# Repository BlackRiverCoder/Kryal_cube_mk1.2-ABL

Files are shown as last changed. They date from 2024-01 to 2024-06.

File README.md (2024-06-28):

# Kryal_cube_mk1.2-ABL

+ Today I am building ABL sensor to 3d printer Kryal Cube mk1.2 
+ In this solution we're using Z Endstop as calibration switch that means, we don't need Z Endstop anymore
+ Calibration will start before every print
+ The disadvantage is that you must install the sensor next to the extruder and after calibration remove it

## Repository architecture:
 - [**Manuals**](#manuals-to-install-abl-on-kryal-cube-mk12)
 - [**Models**](#models)
 - [**Nozzle_to_probe_offset**](#nozzle_to_probe_offset)
 - [**Troubleshooting**](#troubleshooting)
 - [**Sources**](#sources)
 - [**Troubleshooting Sources**](#troubleshooting-sources)

## Manuals to install ABL on Kryal Cube mk1.2:
 
**- 1.)** [English manual](#english-manual)

**- 2.)** [Slovak Manual](#slovak-manual)

## Models:

  - Formats: **.stl** and for SolidWorks **.sldprt**

+ **Right side model used with original extruder: ([ModelR-O v1.0](https://github.com/BlackRiverCoder/Kryal_cube_mk1.2-ABL/tree/main/Assests/Models/ModelR-O%20v1.0))**
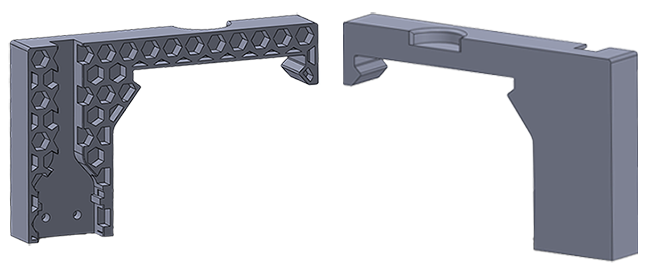
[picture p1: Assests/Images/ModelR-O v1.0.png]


+ **Left side model used with original extruder: ([ModelL-O v1.0](https://github.com/BlackRiverCoder/Kryal_cube_mk1.2-ABL/tree/main/Assests/Models/ModelL-O%20v1.0))**
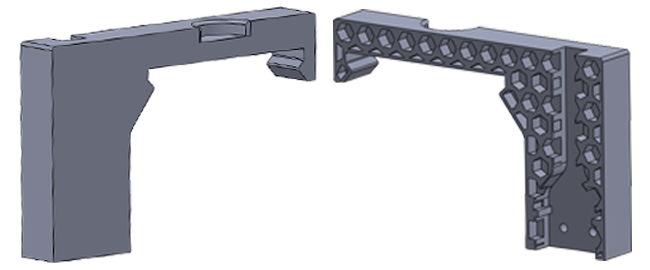
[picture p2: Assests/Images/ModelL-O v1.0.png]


+ **Left side model used with E3D extruder: ([ModelL-E3D v1.0](https://github.com/BlackRiverCoder/Kryal_cube_mk1.2-ABL/tree/main/Assests/Models/ModelL-E3D%20v1.0))**
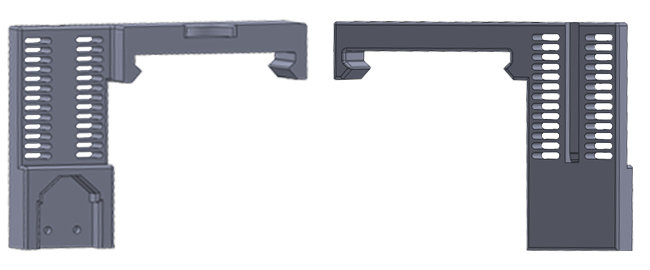
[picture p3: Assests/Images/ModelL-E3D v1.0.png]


+ **Magnetic models used with E3D extruder: ([ModelM-E3D v1.0](https://github.com/BlackRiverCoder/Kryal_cube_mk1.2-ABL/tree/main/Assests/Models/ModelM-E3D%20v1.0))**
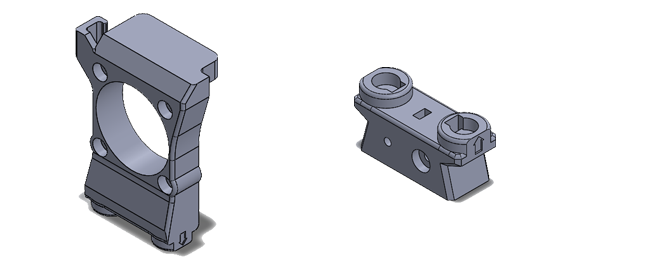
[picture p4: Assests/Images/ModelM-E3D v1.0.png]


## English Manual:

***1.) Hardware preparation:***
 - 1.) **Things we need:**
    - NC Switch
    - Cables
    - Switch holder (according to the side on which the switch will be and according to the extruder type) you can download models [here](https://github.com/BlackRiverCoder/Kryal_cube_mk1.2-ABL/tree/main/Assests/Models) and every model types and images are [here](#models)
    - Some connectors
    - Screws to attach the switch to the holder
    - Magnets 6x3mm (for magnet type ABL)

 - 2.) **Assembling the holder:**
    **Fixed type:**
    - 1.) Solder wires to the C and NC on the switch and at the end of the cable make connector of your choice (as you can see in the red circle (female type))
    - 2.) With the screws attach the switch to the 3d printed model
    - _Your holder should look like this one:_
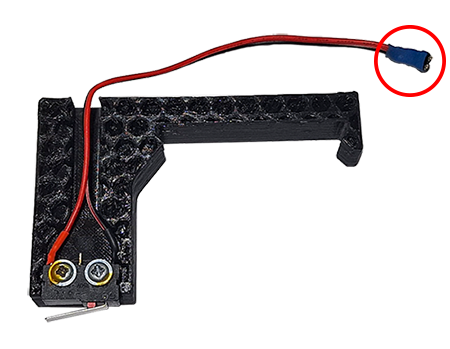
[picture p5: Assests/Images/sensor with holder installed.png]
    

    **Magnet type:**
    - 1.) Insert magnets to both models (Double check the magnet faces, if you don't put them in correct way, they won't snap together)
    - 2.) Attach the microswitch to the microswitch holder and put screws to hold it
    - 3.) Attach cables to the main holder

 - 3.) **Connect cables to the main board:**
    - Pull the cable along 3d printer case, from extruder, where you make another (male type) connector, to the main board
    - Kryal Cube mk1.2 using AtMega2560 with RAMPS14, so connect the switch to these pins:
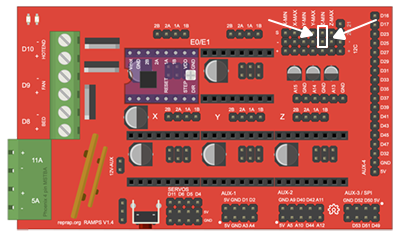
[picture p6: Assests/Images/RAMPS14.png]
   

 - **Final - calibration sensor installed next to the extruder:**
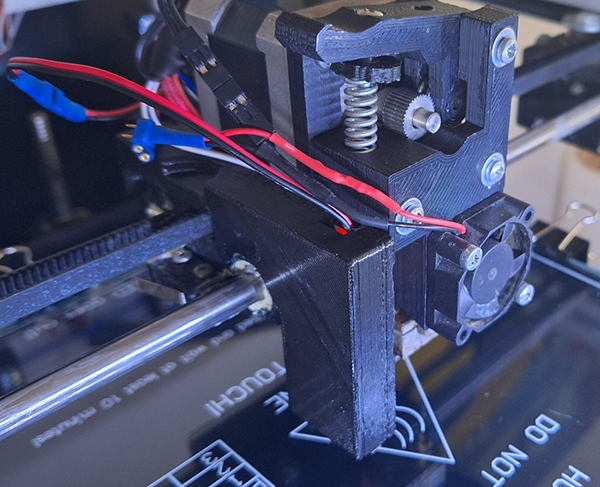
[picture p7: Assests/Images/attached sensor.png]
   

***2.) Firmware configuration:***
 > [!IMPORTANT]
 > Marlin version - 2.0.9.2, in other versions settings can be different.
 - 1.) **Disabling settings:**
   - If you have enabled any of these settings, please disable them using // before every **#define**:
      - **Configuration.h**
        ```
        #define PROBE_MANUALLY
        ```
        ```
        #define AUTO_BED_LEVELING_3POINT
        ```
        ```
        #define AUTO_BED_LEVELING_LINEAR
        ```
        ```
        #define AUTO_BED_LEVELING_UBL
        ```
        ```
        #define MESH_BED_LEVELING
        ```
        ```
        #define RESTORE_LEVELING_AFTER_G28
        ```
        ```
        #define ENABLE_LEVELING_AFTER_G28
        ```
        ```
        #define LCD_BED_LEVELING
        ```
        
      - **Configuration_adv.h**
        ```
        #define BABYSTEP_DISPLAY_TOTAL
        ```
 > [!WARNING]
 > If you don't disable these settings and try to build the code, you can get errors!

 - 2.) **Enabling/configuring settings:**
    - Enable settings removing // before **#define**
      - **Configuration.h**
        - !! Set dimensions where the nozzle is safely on the bed and bed sizes !!
        - EEPROM settings:
          ```
          #define EEPROM_SETTINGS
          ```
          ```
          #define EEPROM_AUTO_INIT
          ```
        - Z Safe homing:
          ```
          #define Z_SAFE_HOMING
          ```
          ```
          #define Z_HOMING_HEIGHT  30
          ```
          ```
          #define Z_AFTER_HOMING   20
          ```
        - ABL:
          - -left +right; -front +back; -down (our solution only has down); these settings can be found [here](#nozzle_to_probe_offset)
          ```
          #define NOZZLE_TO_PROBE_OFFSET { -32, -15, -7 }
          ```
          ```
          #define AUTO_BED_LEVELING_BILINEAR
          ```
          ```
          #define FIX_MOUNTED_PROBE
          ```
          ```
          #define Z_MIN_PROBE_USES_Z_MIN_ENDSTOP_PIN
          ```
          - x*x = number of calibrating points
          ```
          #define GRID_MAX_POINTS_X x
          ```
          - safe distance from each edge of the bed
          ```
          #define PROBING_MARGIN 6
          ```
          ```
          - #define MULTIPLE_PROBING 2
          ```
          - higher speed = more inaccurate calibration
          ```
          #define Z_PROBE_FEEDRATE_SLOW (Z_PROBE_FEEDRATE_FAST / 3)
          ```
          ```
          #define Z_CLEARANCE_DEPLOY_PROBE   10
          ```
          ```
          #define Z_CLEARANCE_BETWEEN_PROBES 10
          ```
          ```
          #define Z_CLEARANCE_MULTI_PROBE     3
          ```
          ```
          #define Z_AFTER_PROBING            30
          ```
          ```       
          #define Z_PROBE_LOW_POINT          -5
          ```

      - **Configuration_adv.h**
        ```
        #define BABYSTEPPING
        ```
        ```
        #define DOUBLECLICK_FOR_Z_BABYSTEPPING
        ```
        ```
        #define BABYSTEP_ZPROBE_OFFSET
        ```
        - This is coreXY 3d printer, so BABYSTEP Graphic Overlay is flipped (Symbol up = bed down; Symbol down = bed up)
        ```
        #define BABYSTEP_ZPROBE_GFX_OVERLAY
        ```
        - When trying to calibrate, on the last line the extruder head was rubbing against the back of the 3d printer frame, so I'm setting the limit from the back side
        ```
        #define PROBING_MARGIN_BACK PROBING_MARGIN +15
        ```
        ```
        #define DEFAULT_STEPPER_DEACTIVE_TIME 400
        ```
      
***3.) Building and flashing the firmware:***
 > [!WARNING]
 > If you have been using the Z Probe settings, reset them via "Configuration", "Restore Settings" and then "Store Settings" on the 3d printer display!
 > You can avoid many problems!

 > [!CAUTION]
 > Flashing the firmware is the most dangerous part, so double-check everything! (Code, USB connection).
 > While flashing, printer must be powered up!

 - 1.) **In VisualCode click build code, if the build is successful, you can write.**

 > [!NOTE]
 > On this printer with AtMega2560 you don't need bootloader, so flash with smile :)
 - 2.) **Now click flash.**
 - 3.) **If the flash was successful, restart the printer.**
 - 4.) **After printer starts up, go to "Configuration", "Restore Setting" and than "Store Settings", with these you store new settings to EEPROM**

***4.) Modify start GCode:***
 + **PrusaSlicer:**
 ```
 M0 Install probe ; Printer will wait until you install probe to the printer

 M140 S[first_layer_bed_temperature] ; Set bed temperature
 M190 S[first_layer_bed_temperature] ; Wait for bed temperature

 G28 ; Home all
 G29 ; Calibration

 M0 Remove probe ; Printer will wait until you remove probe from printer

 M104 S[first_layer_temperature] T0; Set nozzle temperature
 M109 S[first_layer_temperature] T0; Wait for nozzle temperature
 ```

 + **Orca Slicer:**
 ```
 M0 Install probe ; Printer will wait until you install probe to the printer

 M140 S[hot_plate_temp_initial_layer] ; Set bed temp
 M190 S[hot_plate_temp_initial_layer] ; Wait for bed temp

 G28 ; Home all
 G29 ; Calibration

 M0 Remove probe ; Printer will wait until you remove probe to the printer

 M104 S[nozzle_temperature_initial_layer] T0; Set nozzle temp
 M109 S[nozzle_temperature_initial_layer] T0; Wait for nozzle temp
 ```

## Slovak Manual:

***1.) Príprava hardware:***
 - 1.) **Veci, ktoré budeme potrebovať:**
    - NC Spínač
    - Káble
    - Držiak spínača (podľa strany, kde spínač bude a podľa typu extrudera) si môžeš stiahnuť modely [tu](https://github.com/BlackRiverCoder/Kryal_cube_mk1.2-ABL/tree/main/Assests/Models) a pozrieť si každý model s obrázkami [tu](#models)
    - Konektory
    - Šrubky na prichitenie spínača na držiak
    - Magnety 6x3mm (pre magnetický typ ABL)

 - 2.) **Skladanie držiaku snímača:**
    **Pevný typ:**
    - 1.) Prispájkovať káble na C a NC na spínači a na konci kábla urobiť konektor tvojej voľby (viď. červený kruh (female type))
    - 2.) Pomocou šrubiek pripevniť spínač na 3d vytlačený držiak
    - _Malo by to vyzerať nejako takto:_
    

    **Magnetický typ:**
    - 1.) Vlož magnety do obidvoch modelov (Dvakrát skontroluj otočenie magnetov, ak sa dajú opačne, neprichytia sa o seba)
    - 2.) Pripevni microspínač do držiaka microspínača a upevni ho šrubami
    - 3.) Pripevni káble do hlavného modelu

  - 3.) **Pripojenie káblov k základnej doske:**
     - Natiahni káble pozdĺž rámu 3d tlačiarne, od extrudera, kde urobíš opačný konektor pre kábel (male type) k základnej doske
     - Kryal Cube mk1.2 používa AtMega2560 s RAMPS14, takže spínač zapojíme na tieto piny:
     

  - **Ukážka pripevneného senzora vedľa extrudera:**
     

***2.) Configurácia Firmware:***
 > [!IMPORTANT]
 > Marlin verzia - 2.0.9.2, v iných verziách môžu byť nastavenia iné.
 - 1.) **Vypínanie nastavení:**
   - Ak máš v Marline povolené niečo z týchto nastavení, prosím vypni ich pomocou // pred každým **#define**:
      - **Configuraion.h**
        ```
        #define PROBE_MANUALLY
        ```
        ```
        #define AUTO_BED_LEVELING_3POINT
        ```
        ```
        #define AUTO_BED_LEVELING_LINEAR
        ```
        ```
        #define AUTO_BED_LEVELING_UBL
        ```
        ```
        #define MESH_BED_LEVELING
        ```
        ```
        #define RESTORE_LEVELING_AFTER_G28
        ```
        ```
        #define ENABLE_LEVELING_AFTER_G28
        ```
        ```
        #define LCD_BED_LEVELING
        ```

      - **Configuration_adv.h**
        ```
        #define BABYSTEP_DISPLAY_TOTAL
        ```
> [!WARNING]
> Ak nevypneš tieto nastavenia a dáš build code, môžu nastať chyby!

 - 2.) **Povoľovanie/konfigurácia nastavení:**
    - Nastavenia povolíš vymazaním // pred každým **#define**
      - **Configuration.h**
        - !! Nastav veľkosti, kde je tryska bezpečne nad podložkou a veľkosť podložky !!
        - EEPROM nastavenia:
          ```
          #define EEPROM_SETTINGS
          ```
          ```
          #define EEPROM_AUTO_INIT
          ```
        - Z Safe Homing:
          ```
          #define Z_SAFE_HOMING
          ```
          ```
          #define Z_HOMING_HEIGHT  30
          ```
          ```
          #define Z_AFTER_HOMING   20
          ```
        - ABL:
          - -vľavo +vpravo; -dopredu +dozadu; -dole (naše riešenie bude mať hodnotu len -dole, nie hore); tieto nastavenia nájdeš [tu](#nozzle_to_probe_offset)
          ```
          #define NOZZLE_TO_PROBE_OFFSET { -32, -15, -7 }
          ```
          ```
          #define AUTO_BED_LEVELING_BILINEAR
          ```
          ```
          #define FIX_MOUNTED_PROBE
          ```
          ```
          #define Z_MIN_PROBE_USES_Z_MIN_ENDSTOP_PIN
          ```
          - x*x = počet kalibračných bodov
          ```
          #define GRID_MAX_POINTS_X x
          ```
          - bezpečná vzdialenosť od každého kraja podložky
          ```
          #define PROBING_MARGIN 6
          ```
          ```
          - #define MULTIPLE_PROBING 2
          ```
          - vyššia rýchlosť = menej presná kalibrácia
          ```
          #define Z_PROBE_FEEDRATE_SLOW (Z_PROBE_FEEDRATE_FAST / 3)
          ```
          ```
          #define Z_CLEARANCE_DEPLOY_PROBE   10
          ```
          ```
          #define Z_CLEARANCE_BETWEEN_PROBES 10
          ```
          ```
          #define Z_CLEARANCE_MULTI_PROBE     3
          ```
          ```
          #define Z_AFTER_PROBING            30
          ```
          ```       
          #define Z_PROBE_LOW_POINT          -5
          ```

      - **Configuration_adv.h**
        ```
        #define BABYSTEPPING
        ```
        ```
        #define DOUBLECLICK_FOR_Z_BABYSTEPPING
        ```
        ```
        #define BABYSTEP_ZPROBE_OFFSET
        ```
        - Keďže táto tlačiareň je coreXY, BABYSTEP Graphic Overlay je otočený (Symbol hore = bed dole; Symbol dole = bed hore)
        ```
        #define BABYSTEP_ZPROBE_GFX_OVERLAY
        ```
        - Pri pokuse o kalibráciu sa na poslednom riadku hlava extrudéra otierala o zadnú časť rámu 3d tlačiarne, takže nastavujem limit zo zadnej strany
        ```
        #define PROBING_MARGIN_BACK PROBING_MARGIN +15
        ```
        ```
        #define DEFAULT_STEPPER_DEACTIVE_TIME 400
        ```

***3.) Build a flashovanie firmware:***
 > [!WARNING]
 > Ak si používal Z Probe nastavenia, resetuj ich cez "Configuration", "Restore Settings" a potom "Store Settings" na displeji 3d tlačiarne!
 > Zabrániš tak veľa problémom!

 > [!CAUTION]
 > Flashovanie firmware je tá najbezpečnejšia časť, takže všetko 2-krát skontroluj (Kód, USB pripojenie)
 > Počas flahovania musí byť tlačiareň napájaná!
  
 - 1.) **Vo VisualCode klikni na build code, ak bol build úspešný, môžeš flashovať.**

 > [!NOTE]
 > Na tejto tlačiarni s AtMega2560 nepotrebuješ bootloader, takže flashuj s úsmevom :)
 - 2.) **Teraz klikni na flash.**
 - 3.) **Ak bol flash úspešný, reštartuj tlačiareň.**
 - 4.) **Po reštarte tlačiarne choď do "Configuration", "Restore Settings" a potom "Store Settings", takto uložíš nové dáta do pamäte EEPROM**

***4.) Modifikácia GCode:***
 + **PrusaSlicer:**
 ```
 M0 Vlozit senzor ; Printer will wait until you install probe to the printer

 M140 S[first_layer_bed_temperature] ; Set bed temperature
 M190 S[first_layer_bed_temperature] ; Wait for bed temperature

 G28 ; Home all
 G29 ; Calibration

 M0 Odstranit senzor ; Printer will wait until you remove probe from printer

 M104 S[first_layer_temperature] T0; Set nozzle temperature
 M109 S[first_layer_temperature] T0; Wait for nozzle temperature
 ```

 + **Orca Slicer:**
 ```
 M0 Vlozit senzor ; Printer will wait until you install probe to the printer

 M140 S[hot_plate_temp_initial_layer] ; Set bed temp
 M190 S[hot_plate_temp_initial_layer] ; Wait for bed temp

 G28 ; Home all
 G29 ; Calibration

 M0 Odstranit senzor ; Printer will wait until you remove probe to the printer

 M104 S[nozzle_temperature_initial_layer] T0; Set nozzle temp
 M109 S[nozzle_temperature_initial_layer] T0; Wait for nozzle temp
 ```

## Nozzle_to_probe_offset:
**[ModelL-O v1.0](https://github.com/BlackRiverCoder/Kryal_cube_mk1.2-ABL/tree/main/Assests/Models/ModelL-O%20v1.0) with original (old) extruder:**
 - -left +right; -front +back; -down (our solution only has down);
  - Switch is 32mm left from the nozzle, so the first value will be **-32**
  - Switch is 15mm back from the nozzle, so the second value will be **-15**
  - Switch is 7mm under the nozzle, so the third value will be **-7**
  ```
  #define NOZZLE_TO_PROBE_OFFSET { -32, -15, -7 }
  ```

**[ModelL-E3D v1.0]() with E3D extruder:**
 - -left +right; -front +back; -down (our solution only has down);
  - Switch is 36mm left from the nozzle, so the first value will be **-36**
  - Switch is 10mm back from the nozzle, so the second value will be **-10**
  - Switch is 13mm under from the nozzle, so the third value will be **-13**
  ```
  #define NOZZLE_TO_PROBE_OFFSET { -36, -10, -13 }
  ```
 > [!TIP]
 > For E3D extruder you can change this setting in **Configuration_adv.h** to +10:
  ```
  #define PROBING_MARGIN_BACK PROBING_MARGIN +10
  ```

## Troubleshooting:

***M112 Printer Halted - Probing Failed:***
 - 1.) **Make manual calibration of the bed corners and start the calibration once again.**
 > [!TIP]
 > You can enable Bed Tramming in Marlin, so the printer goes to every corner of the bed to infinity:
>#define LEVEL_BED_CORNERS
 - 2.) **Disable Multiple Probing**
   ```
   #define MULTIPLE_PROBING
   ```

***When the bed is too low, homing cannot be performed:***
 - **Use G28 X Y and G28 Z separately, instead of G28**

## Sources:
- https://www.youtube.com/watch?v=HJV82NHOY-0&
- https://www.youtube.com/watch?v=NTvjIOFMs6M

## Troubleshooting sources
- https://www.youtube.com/watch?v=t4tNSk1_Sc8
- https://www.reddit.com/r/ender3v2/comments/uq3aq3/bed_not_pressing_limit_switch_when_auto_homing/
- https://forum.drucktipps3d.de/forum/thread/14381-probe-failed-with-g29-after-initial-installation/
- https://www.3dprintgorilla.com/marlin-firmware-m112-shutdown/
- https://github.com/MarlinFirmware/Marlin/issues/21118
- https://www.reddit.com/r/3Dprinting/comments/ubwuvu/getting_mad_with_bed_size_and_margins_in_marlin/
- https://github.com/MarlinFirmware/Marlin/issues/18033
- https://www.reddit.com/r/ender3v2/comments/mtfxj3/firmware_crash_error_probing_failed/
- https://www.reddit.com/r/ender3/comments/nc2ul2/bltouch_probe_doesnt_touch_bed_on_first_point/
- https://www.reddit.com/r/3Dprinting/comments/g5a4mz/bltouch_not_probing_bed_g29_but_z_homing_works/

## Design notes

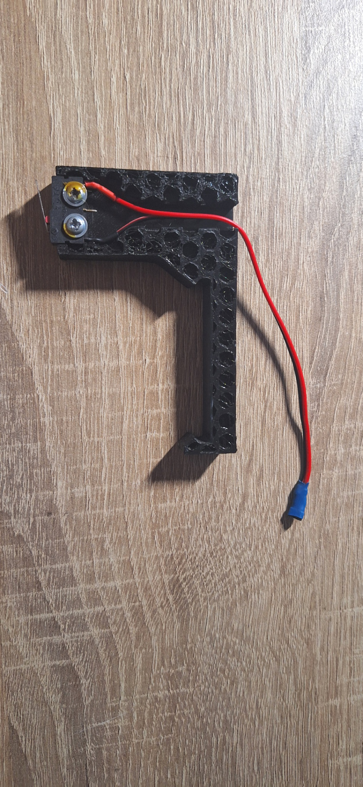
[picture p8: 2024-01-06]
Assests/Images/sensor.jpg

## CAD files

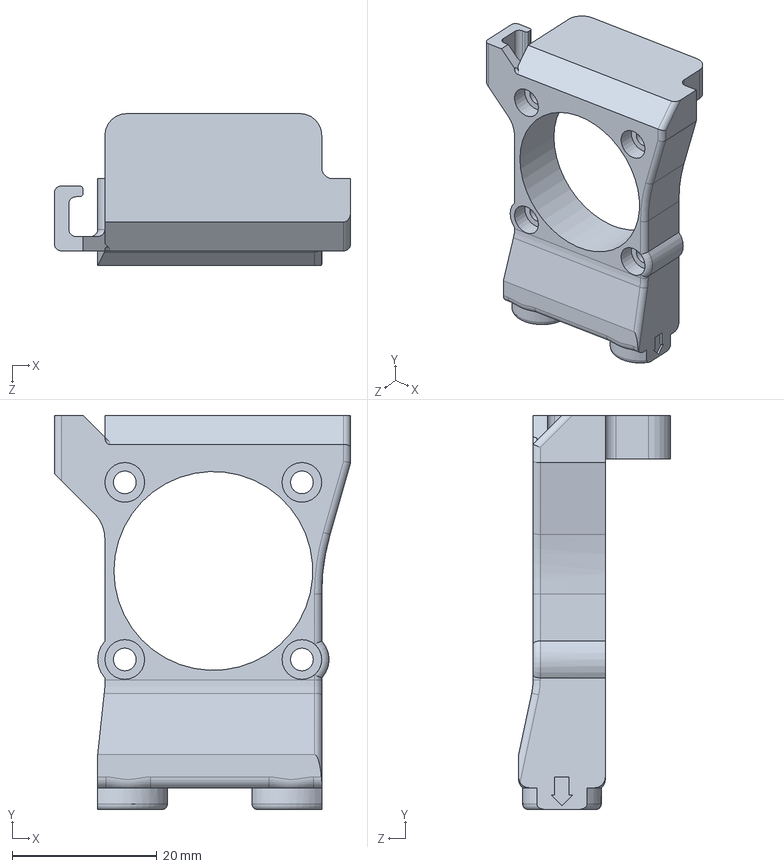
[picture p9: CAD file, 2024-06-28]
Assests/Models/ModelM-E3D v1.0/ModelM-E3D v1.0 - MainHolder.SLDPRT
41.0 x 54.5 x 21.0 mm

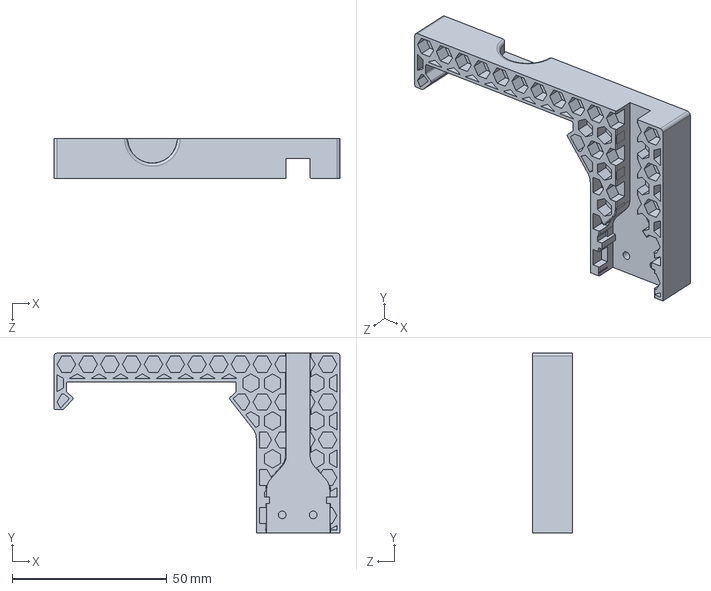
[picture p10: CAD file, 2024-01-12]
Assests/Models/ModelL-E3D v1.0/ModelL-E3D v1.0.SLDPRT
92.3 x 58.0 x 13.0 mm

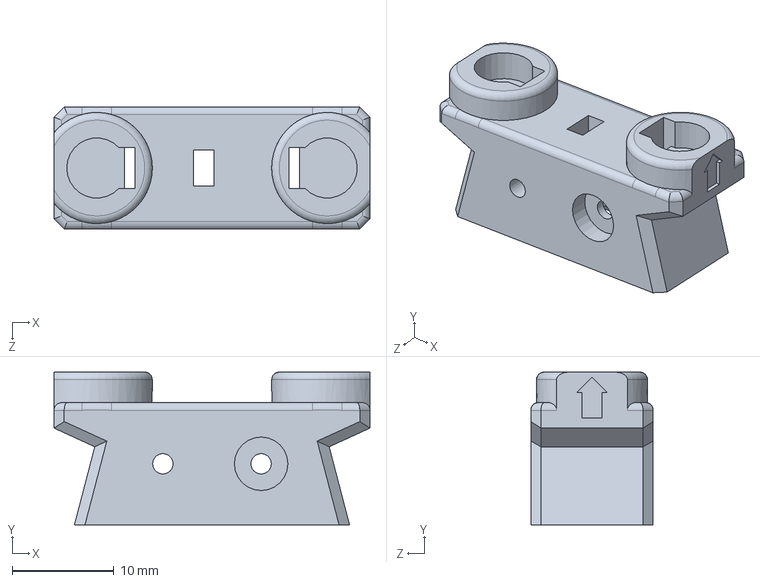
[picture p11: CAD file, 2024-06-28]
Assests/Models/ModelM-E3D v1.0/ModelM-E3D v1.0 - MicroswitchHolder.SLDPRT
31.0 x 15.0 x 12.0 mm

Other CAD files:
Assests/Models/ModelL-O v1.0/ModelL-O v1.0.STL
Assests/Models/ModelR-O v1.0/ModelR-O v1.0.SLDPRT
Assests/Models/ModelL-E3D v1.0/ModelL-E3D v1.0.STL
Assests/Models/ModelM-E3D v1.0/ModelM-E3D v1.0 - MainHolder.STL
Assests/Models/ModelM-E3D v1.0/ModelM-E3D v1.0 - MicroswitchHolder.STL
Assests/Models/ModelR-O v1.0/ModelR-O v1.0.STL
